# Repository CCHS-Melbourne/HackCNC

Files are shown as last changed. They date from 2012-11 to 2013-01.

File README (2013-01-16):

This repository is for the HackCNC project files.

HackCNC is a low-cost 2axis CNC machine developed for LCA2013 - Canberra.

It was developed and produced by members of hackmelbourne.org and freetronics.com.au

Hardware contains the development files for building the hackCNC frame.

Software contains the development and config files to compile the source code for the arduino and connect linuxcnc.

Docs has several documents and images that will help when assembling the kit.

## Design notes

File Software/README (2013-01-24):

This folder contains software elements useful in working with the HackCNC project. 

Libraries contains the arduino libraries needed to compile the EMCAruino sketch.

EMCArduino_07b_32u4 is the development firmware compatible with an Arduino based on a AT32u4 micro

NewLiquidCrystal is a control driver for using the attached LCD panel.

digitalWriteFast is a fast pin manipulation commands.

my-mill contains the connection and configuration files linuxcnc uses to connect to the arduino.  The simpilest place to put this in your home directory, then run linuxcnc with the command `linuxcnc my-mill.ini`

FunctionTest contains a basic sketch for testing high level components (serial communications, LCD, steppers, servo) without LinuxCNC.

----------
This software is based on the work of others. Attribution and other information can be found as follows:
digitalWriteFast - http://code.google.com/p/digitalwritefast/
EMCArduino - http://emc2arduino.wordpress.com/
LinuxCNC - http://www.linuxcnc.org/
NewLiquidCrystal - https://github.com/marcmerlin/NewLiquidCrystal

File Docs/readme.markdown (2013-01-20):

hackCNC

Conceptual Overview:


[Wiki page with assembly tips](http://www.arduinominiconf.org/index.php/HackCNC_Assembly_Tips)

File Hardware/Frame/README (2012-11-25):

These are the design files for the hackCNC project's frame.

This frame was designed to work with a material 6mm in depth.

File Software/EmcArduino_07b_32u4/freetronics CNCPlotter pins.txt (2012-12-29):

These are the pinouts for the Freetronics CNCPlotter board developed by Luke Weston.
This board is built around an Arduino Leonardo chip.
By default, the board is set to 8x microstepping.  This can be changed by soldering headers on the 3 pads for each driver board.
The CNCPlotter board only has two stepper drivers, with a servo for it's third axis.  An additional driver board can be connected to D5 and D13.

D0: UART RXD (not used, broken out to spare header)
D1: UART TXD (not used, broken out to spare header)
D2: LCD Strobe (Data loaded serially from AVR into 8-bit latch. Same as Pebble LCD hardware.)
D3: LCD Data
D4: LCD Clock
D5: Z-axis direction (not used in most cases)
D6: SD Card SPI chip select (active low). Standard SPI hardware (MOSI, MISO, SCK) used for SPI communications with SD card.
D7: Z-axis limit switch input (not used in most cases)
D8: Y-axis step signal
D9: Y-axis direction signal
D10: X-axis step signal
D11: X-axis direction signal
D12: Servo motor PWM position signal
D13: Z-axis step signal (not used usually)

A0: Touchscreen 1
A1: Touchscreen 2
A2: Touchscreen 3
A3: Touchscreen 4
A4: Y-axis limit switch input
A5: X-axis limit switch input

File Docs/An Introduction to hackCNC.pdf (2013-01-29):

## An Introduction to hackCNC

or -
hackCNC, a gateway drug for makers

or -
"What the hell is that whining noise?" - spouses everywhere

Presented by John Spencer - Linux Conf Australia - Canberra 2013

### What is hackCNC

hackCNC is a low cost, open source, two axis plotter.

It is desktop sized.

It is controlled by an Arduino processor and LinuxCNC.

It is cheap. This is important.

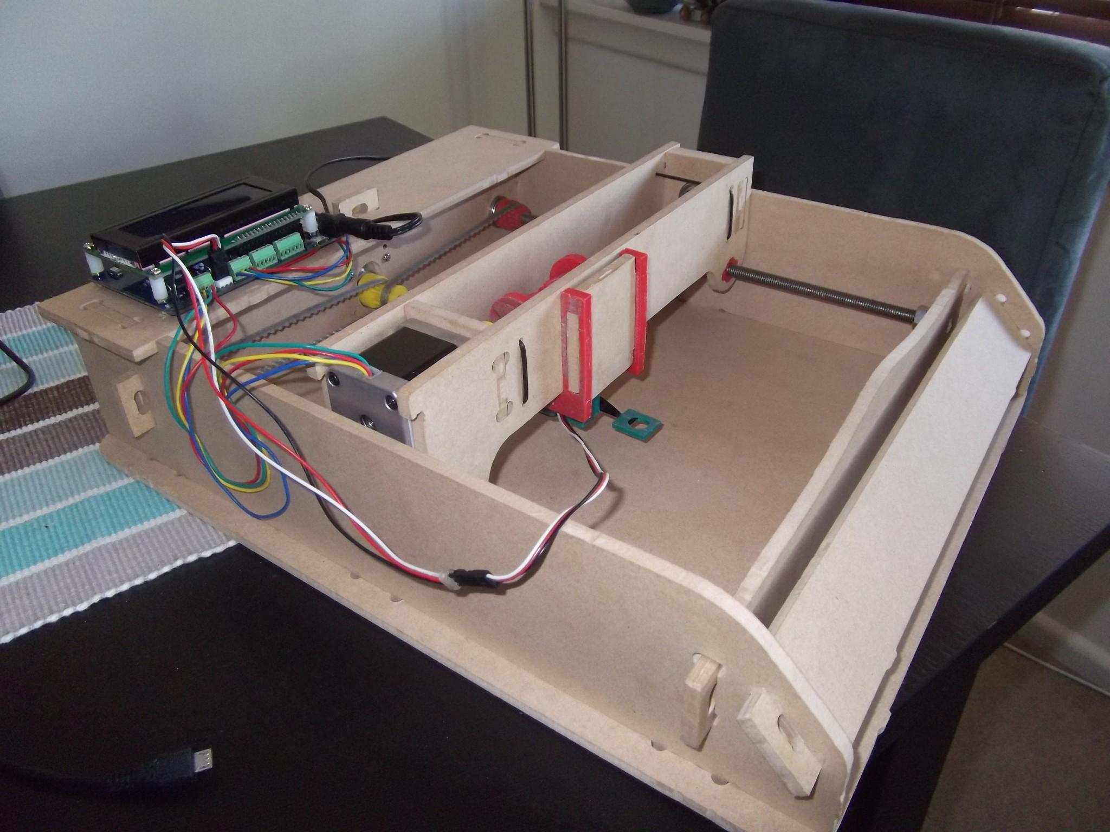
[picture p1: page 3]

### Why design/build something like hackCNC?

To get people interested in CNC.

To have something fun for groups like this one to build.

To give schools or special interest groups a nice easy project to work on.

### Limitations

Only 2 axis.
Threaded rods are a rough. Slow.
Noisy.
Small build area.
Only 50mm of vertical space.
3D parts take ~3.5 hours to make.

### How it was made - Frame

Designed on a completely not Open Source piece of software, let's call it Screw-up.

gCode generated on a different, also completely not Open Source piece of software, let's call that ... CAM-thingy.

Cut on my sort of Open Source home built CNC Router, running the totally FOSS linuxCNC.org!

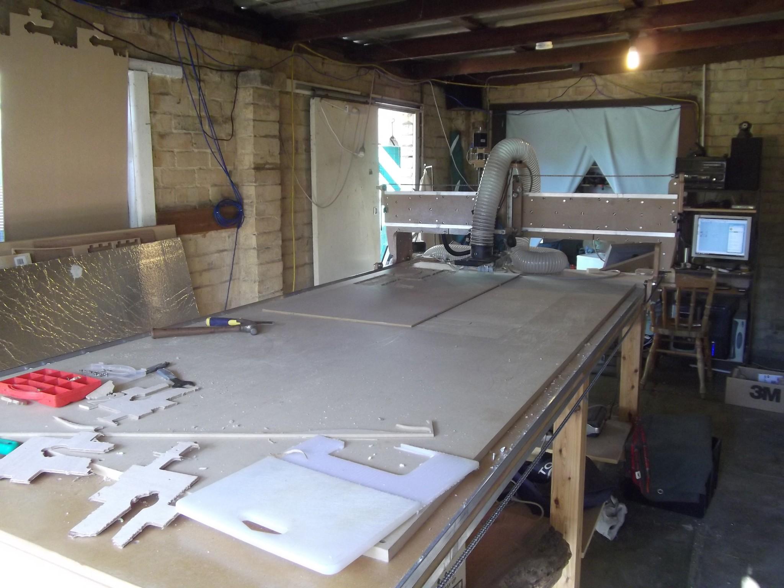
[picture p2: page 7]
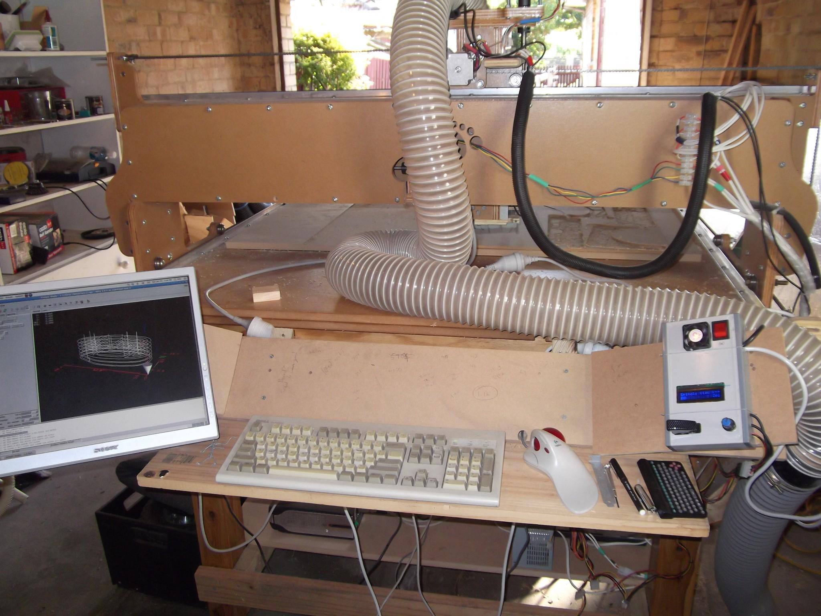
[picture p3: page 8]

### How it was made - Plastic

Also designed using Screw-up.

Cut into gCode using either slic3r.org or Cura.

Generously printed by members of the Melbourne Hackerspace. Mainly using Prusa 3D printers because they have a large enough build platform.

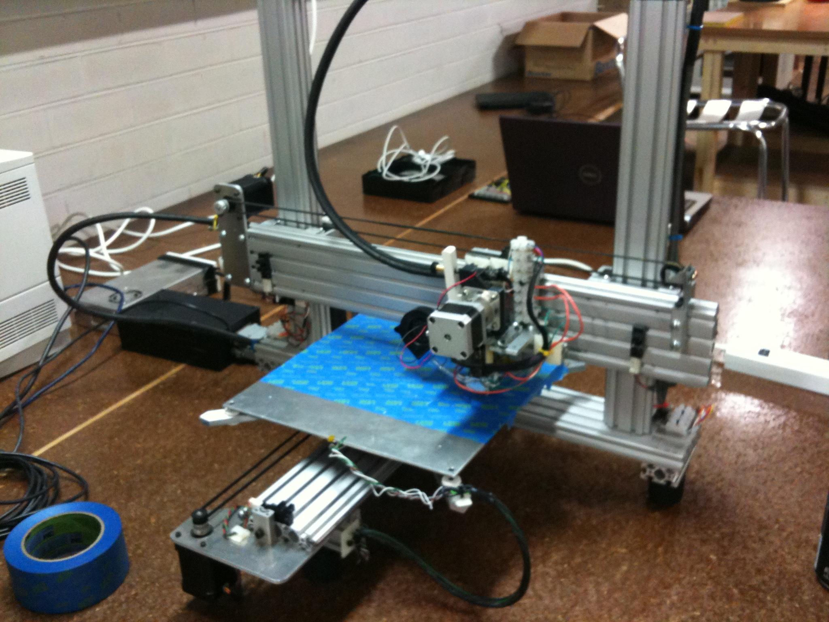
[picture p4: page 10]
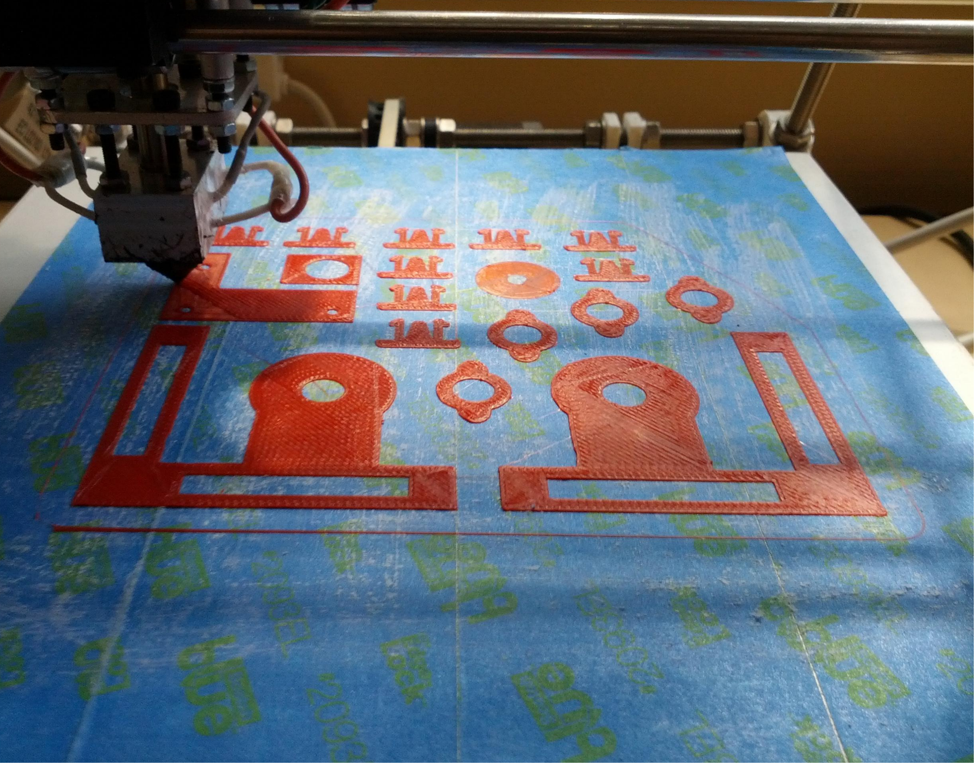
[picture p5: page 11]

### How it was made -Electronics/CNCPlot

Custom board designed by Luke Weston around the Arduino 32u4 (Leonardo) chip.

I'll let him talk about that.

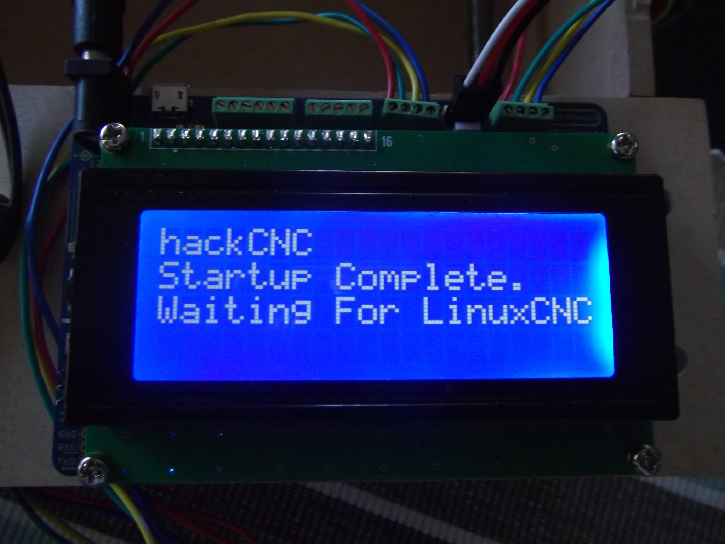
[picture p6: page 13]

### How it was made - all the other bits

Sourced by other Melbourne Hackerspace members, mostly from China and the US.

Software - How to make it do something.

Draw your plan in your favourite drawing program and load it into Inkscape.

Use the Export gCode tool. A negative Z axis movement of -0.8 works best.

Load your file in LinuxCNC.

### Great, NOW what do I do with it?

Just a few ideas I've heard :)

Frikken Laser Beams!!! (Sharks sold separately) Rotary Engraver.
Drag Cutter.
Two Colours.
Proper 3-axis (there is a breakout board) PCB engraving.
Simple 3D touch mapping.
Replace the threaded rod with belts and rails.
-- and, of course, you can re-use the electronics...

Contributors......so far.....

A big thank you to everyone who helped make this project possible. Here are most of the people who made this happen (I know I've missed some people....)

Freetronics/Jon Oxer
John Bosua
John Spencer
Luke Weston
Rob Brittain
Michael Sullivan
Andy Gelme
Bob Powers

Stuart Young
Angus Gratton
Don Douwsma
Ken Ihara
Josh Mesilane
Grant Diffey
George Patterson

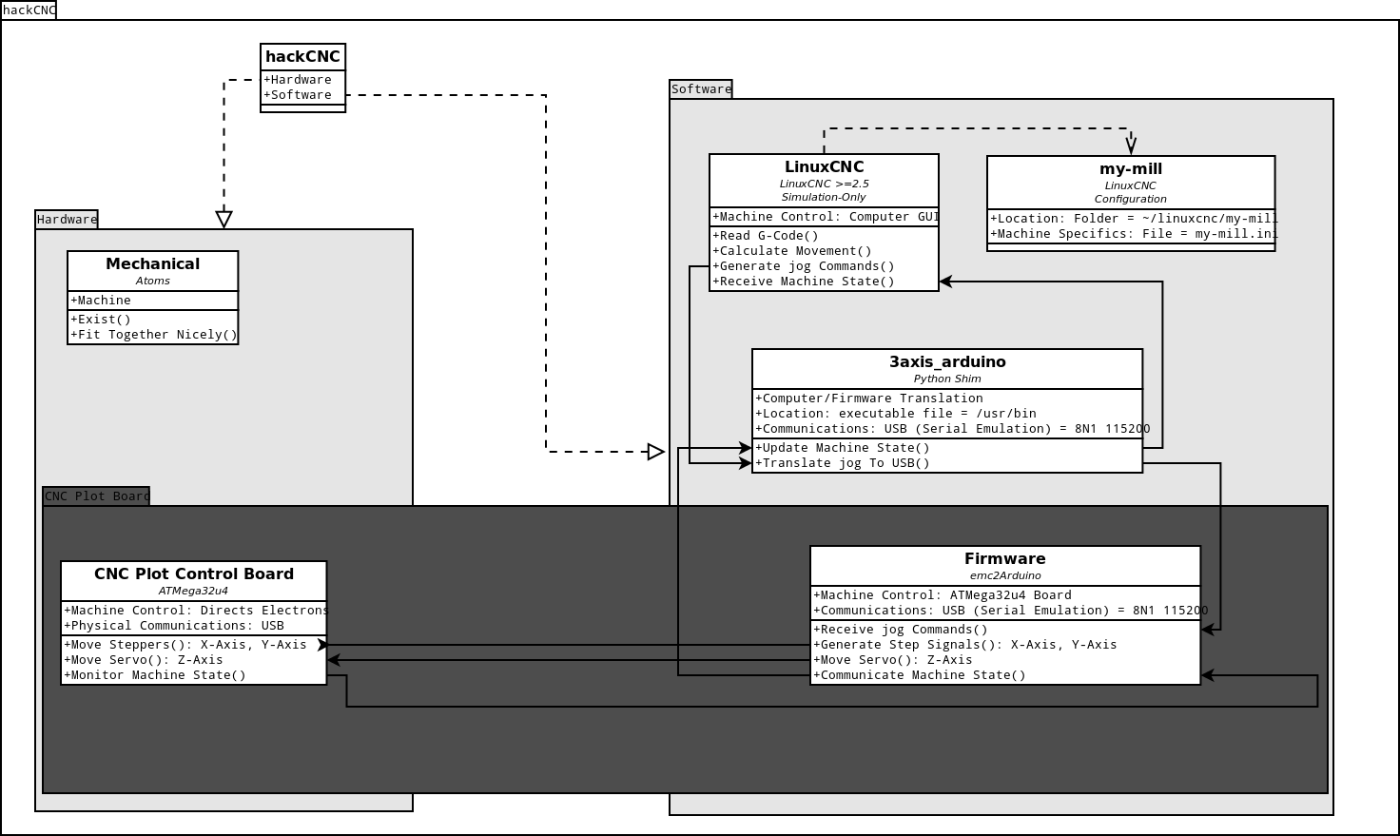
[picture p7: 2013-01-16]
Docs/Overview.png

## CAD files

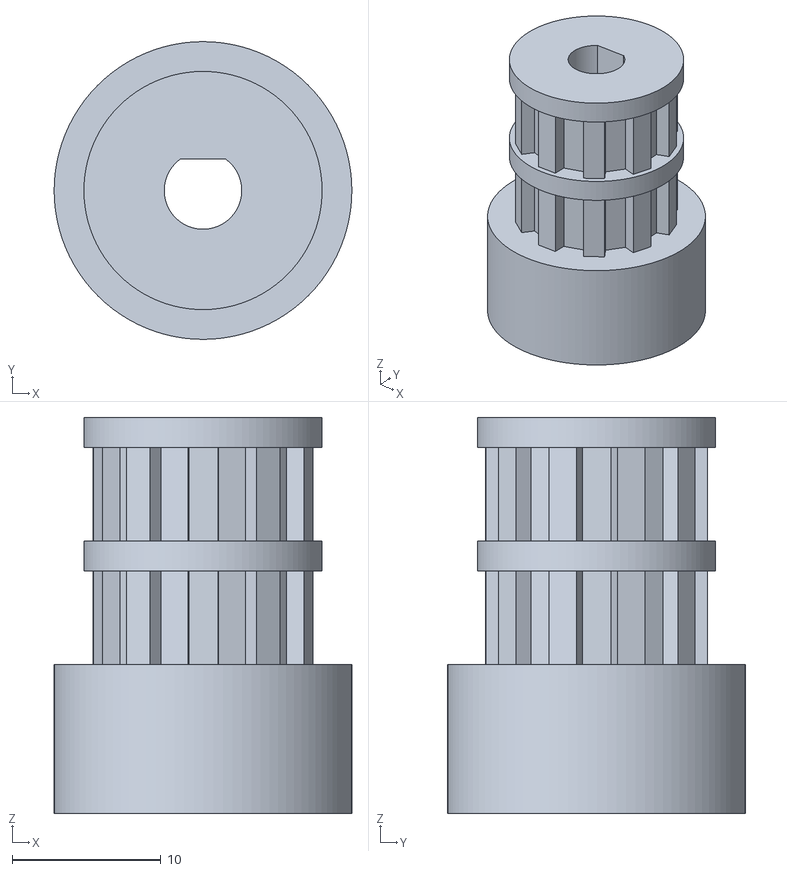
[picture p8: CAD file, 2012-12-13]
Hardware/3D Prints/5mm pulley.stl
20.0 x 20.0 x 26.6

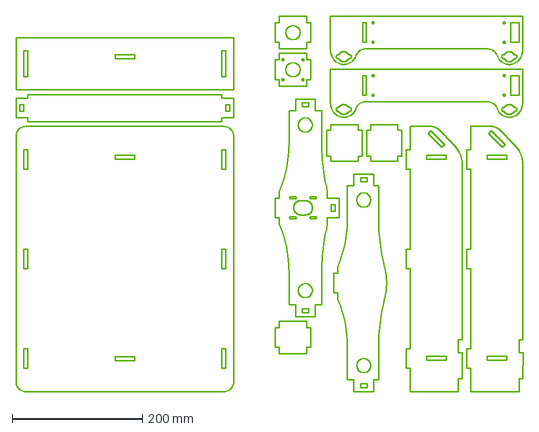
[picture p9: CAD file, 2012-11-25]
Hardware/Frame/hackCNC.dxf
778.0 x 576.0 mm

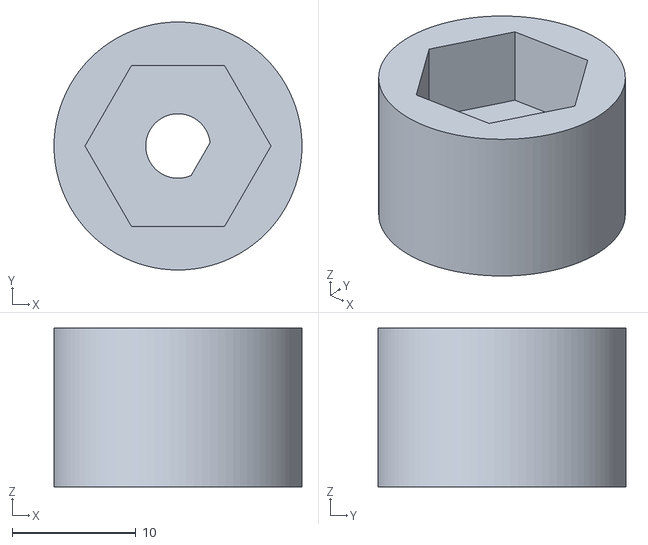
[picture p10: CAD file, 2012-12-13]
Hardware/3D Prints/shaft adapter.stl
20.0 x 20.0 x 12.8

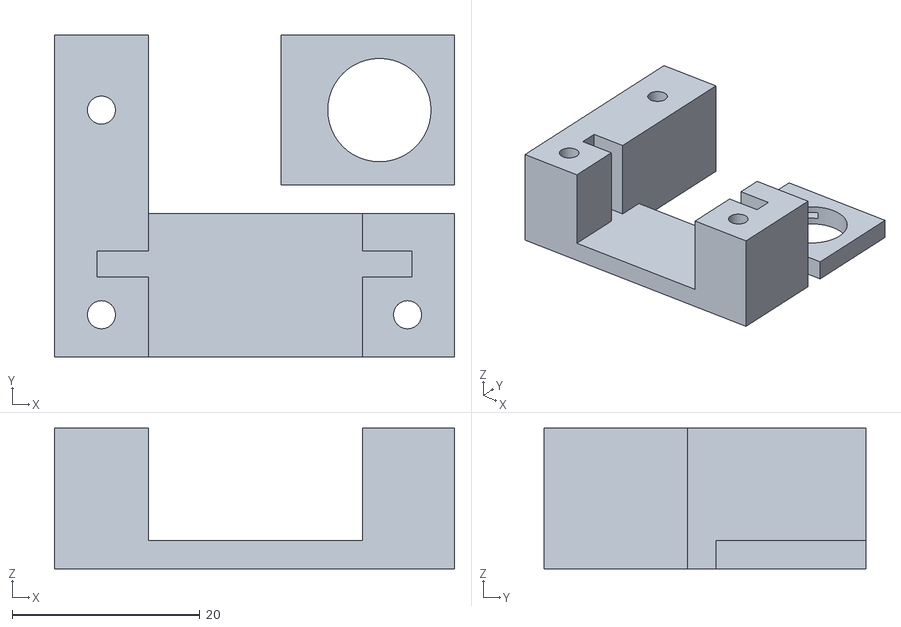
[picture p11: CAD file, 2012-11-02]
Hardware/3D Prints/Servo Holder-1.1.stl
42.6 x 34.3 x 15.0

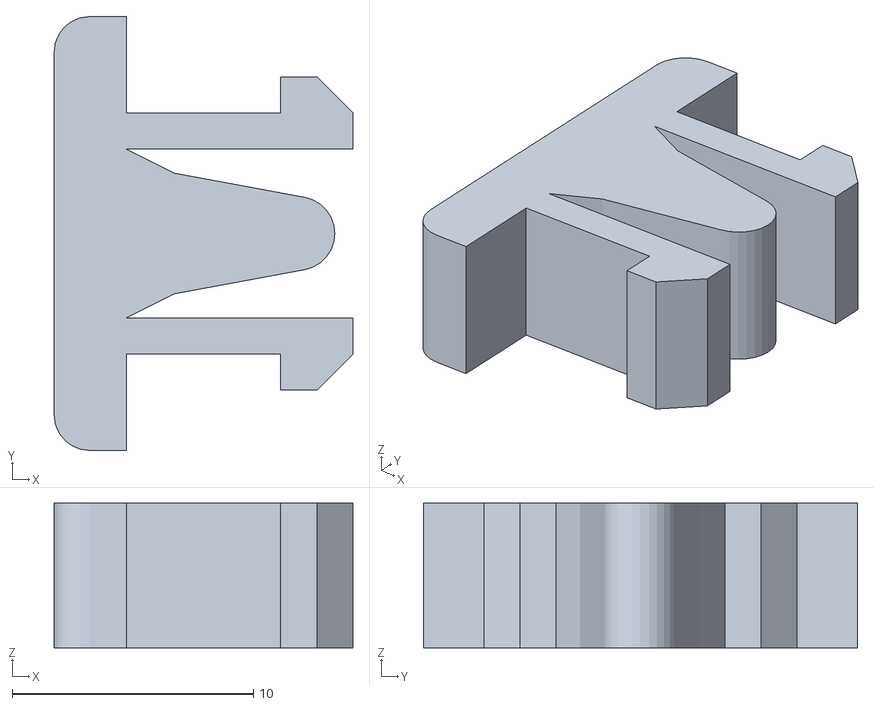
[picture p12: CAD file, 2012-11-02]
Hardware/3D Prints/Holding Pin.stl
12.4 x 18.0 x 6.00

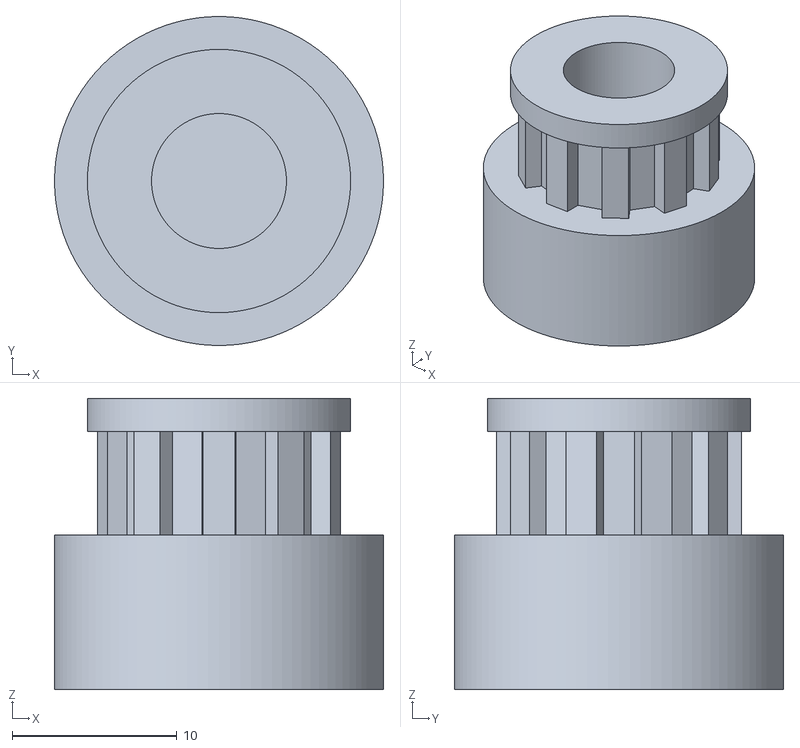
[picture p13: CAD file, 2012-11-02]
Hardware/3D Prints/8mm pulley.stl
20.0 x 20.0 x 17.7

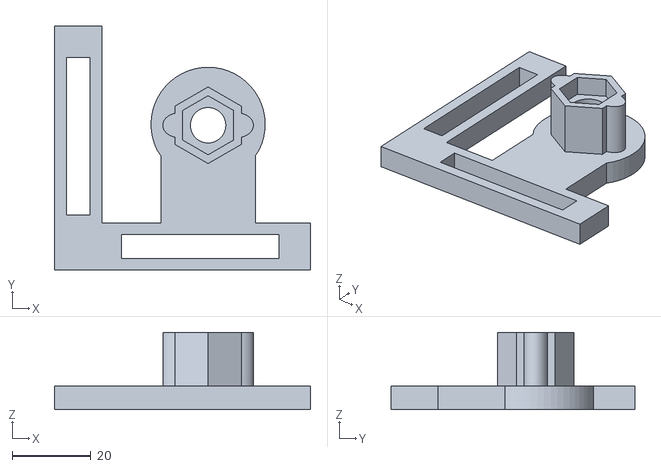
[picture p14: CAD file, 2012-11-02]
Hardware/3D Prints/Carriage 2.stl
65.0 x 62.0 x 19.6

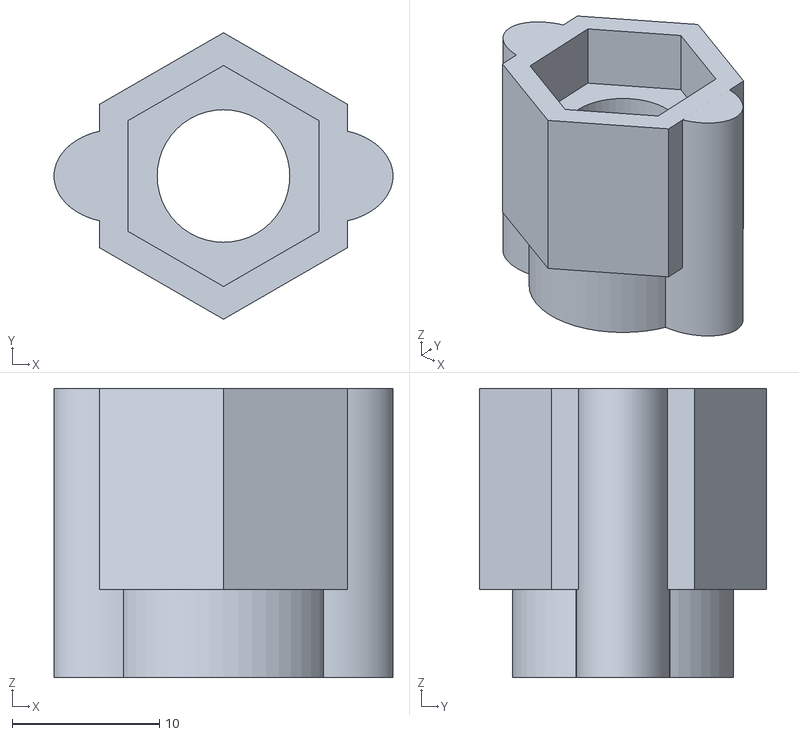
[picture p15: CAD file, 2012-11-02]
Hardware/3D Prints/Nut holder.stl
23.0 x 19.5 x 19.6

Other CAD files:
Hardware/3D Prints/Carriage 1.stl

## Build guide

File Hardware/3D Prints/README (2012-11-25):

"3D Print" quantities :-
1x 5mm pulley.stl
2x 8mm pulley.stl
1x Carriage 1.stl
1x Carriage 2.stl
9x Holding Pin.stl
4x Nut holder.stl
1x Servo Holder-1.1.stl
1x shaft adapter.stl

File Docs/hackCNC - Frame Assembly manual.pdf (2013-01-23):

## hackCNC

Frame Assembly Manual

Hints
1. If parts don't fit, first try turning them 90 degrees. A lot of them look square, but are actually rectangles (blame the designer).
2. Don't be afraid to try some brute force and ignorance. A lot of these parts are a VERY tight fit.
3. The wires on the stepper motors should be facing UP.
4. Without superglue on the nuts, this won't work. But don't worry, a pair of pliers will break the bond so you can break your hackCNC down for your trip home.

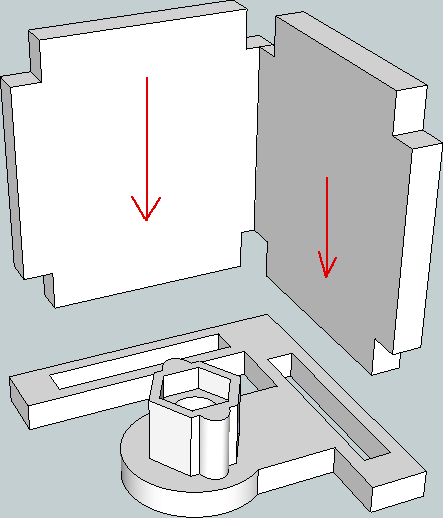
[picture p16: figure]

Section 1 : Z Axis Carriage | Section 1 : Step 1
| Parts 1 x 3D Printed Z Axis Bracket 2 x CNC Z Axis Plate

Section 1 : Step 2

Parts

1 x 8mm Long Nut

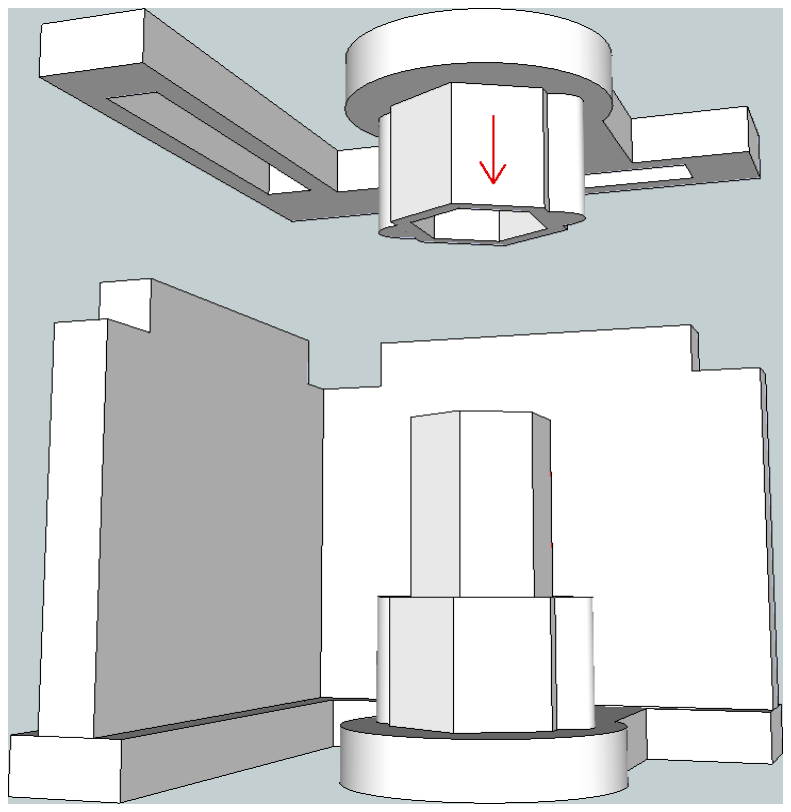
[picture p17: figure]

Section 1 : Step 3

Parts

1 x 3D Printed Z Axis Bracket

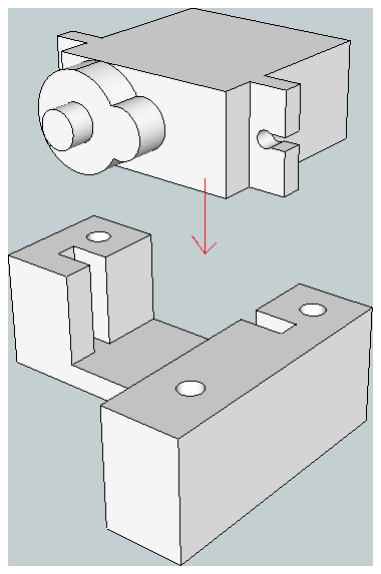
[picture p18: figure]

Section 1 : Step 4

Parts

1 x 3D Printed Servo Bracket 1 x 9g microservo

Section 1 : Step 5

Parts

2 x 4g Wood Screw

Section 1 : Step 6

Parts

1 x 4g Wood Screw
1 x Spring

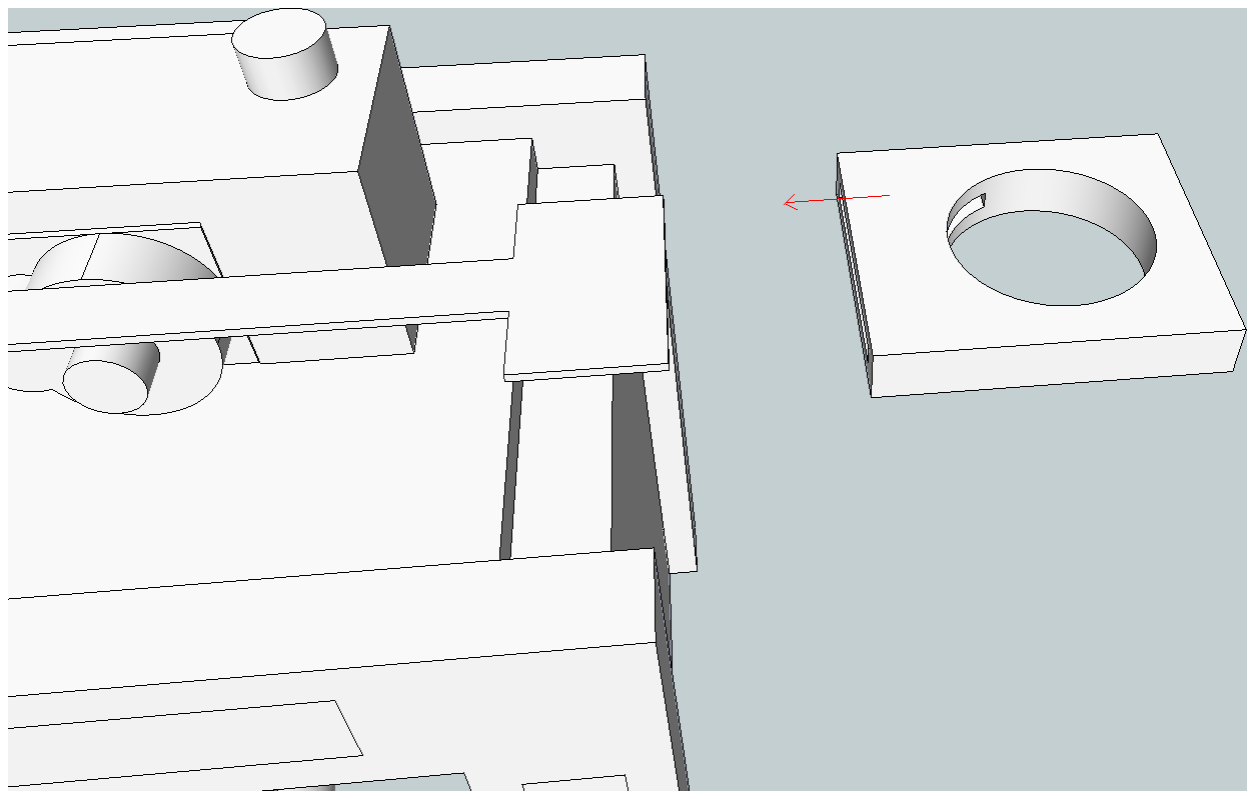
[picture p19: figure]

Section 1 : Step 7

Parts

1 x 3D Printed Pen Holder

Section 1 : Complete! | Section 2 : Y Axis Carriage

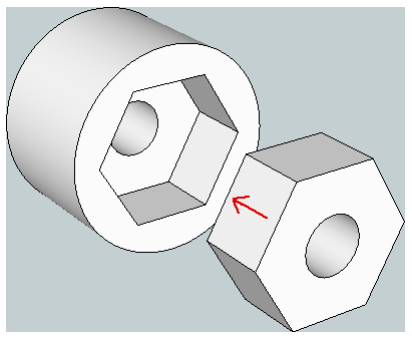
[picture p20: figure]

Section 2 : Step 1

Parts

1 x 3D Printed Y Axis Coupler 1 x 8mm nut

Section 2 : Step 2

Parts

1 x Nema 17 Stepper Motors 1 x CNC Y Axis Motor Mount 4 x 3mm Machine Screws

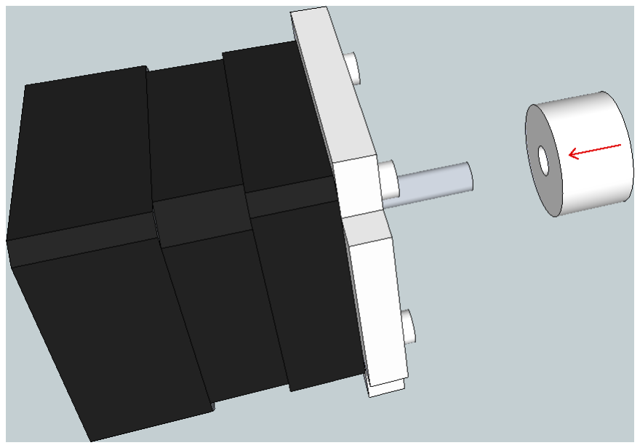
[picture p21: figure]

Section 2 : Step 3 | Section 2 : Step 4
| Parts 1 x 210 mm Long 8mm all-thread Part from Section 1

Section 2 : Step 4 - complete | Section 2 : Step 5
| Parts 1 x 8mm nuts Part from Section 2 : Step 4

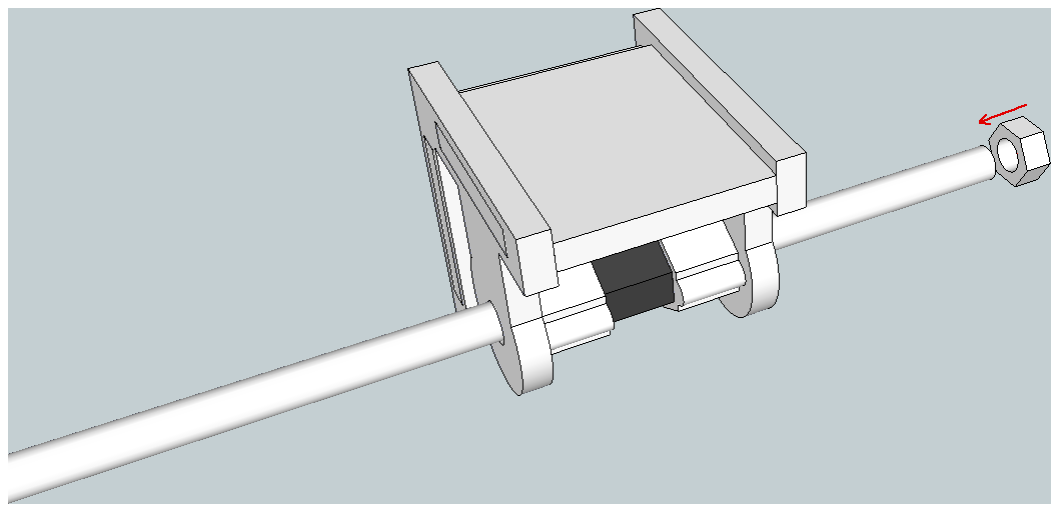
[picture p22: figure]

Section 2 : Step 6

Parts

1 x CNC Carriage Side
Part from Section 2 : Step 3

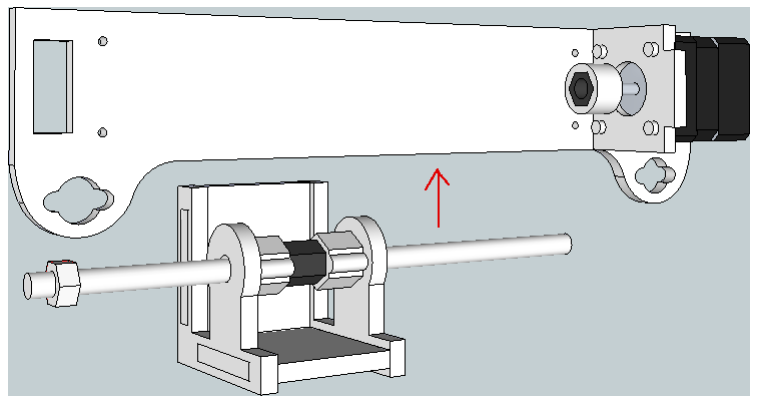
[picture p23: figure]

Section 2 : Step 7

Section 2 : Step 8

Superglue the end of the rod where it goes into the nut

Section 2 : Step 9

Parts

1 x CNC Y Axis Bearing Mount 1 x 608 bearing

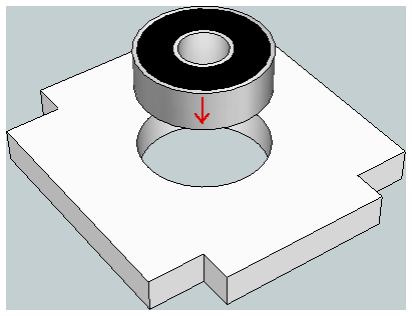
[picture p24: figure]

Section 2 : Step 10

Place an 8mm washer between the bearing and nut (not shown)

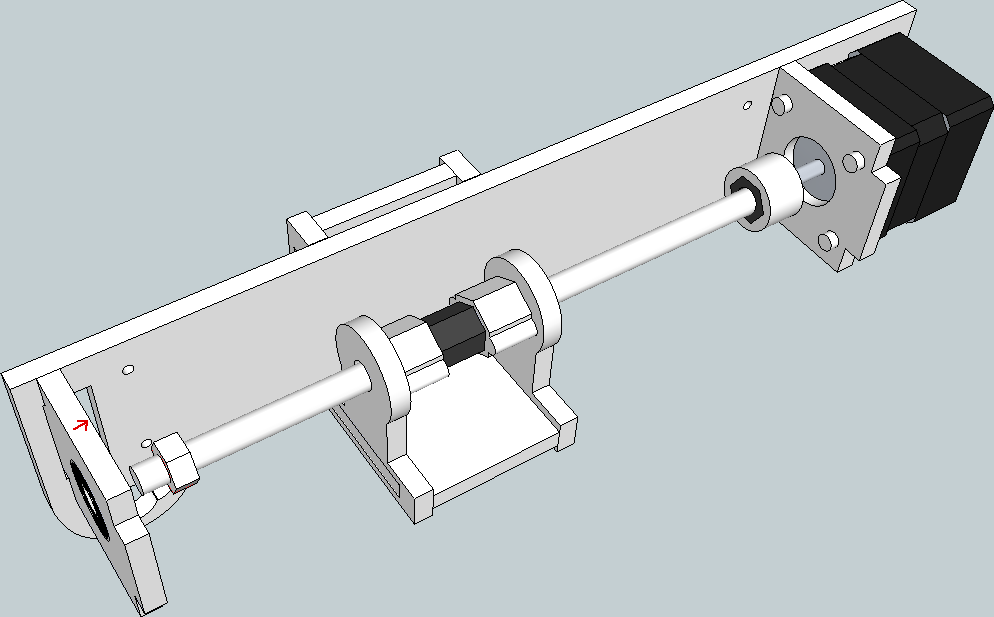
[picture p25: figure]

Section 2 : Step 11

Section 2 : Step 12

Parts

1 x CNC Y Axis Mount

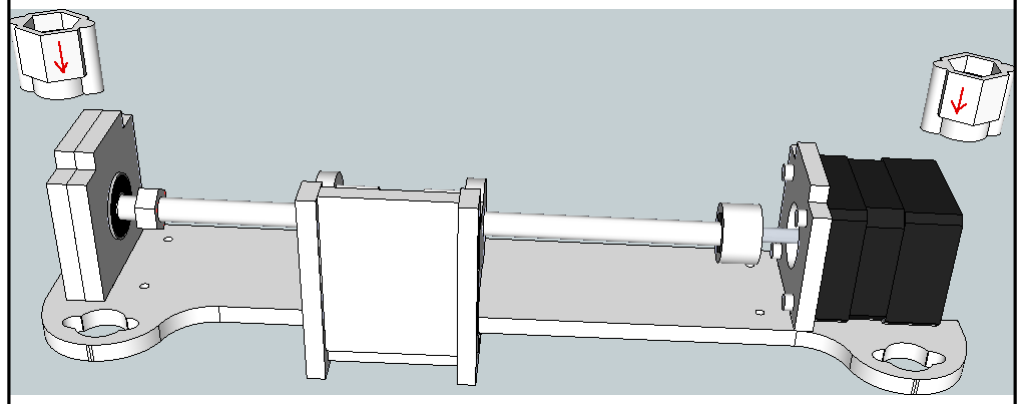
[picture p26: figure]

Section 2 : Step 13

Parts

2 x 3D Printed X Axis Nut Bracket

Section 2 : Step 14

Parts

2 x 8mm Long Nut

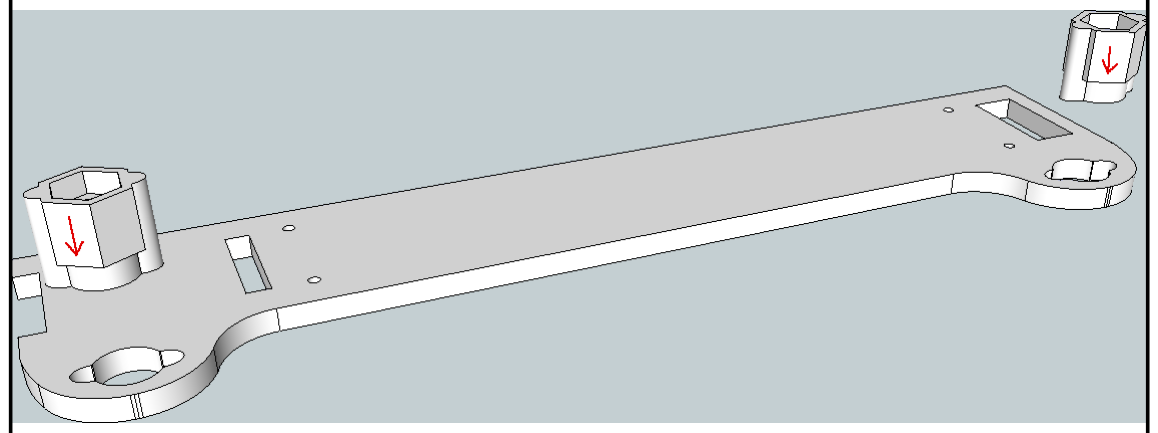
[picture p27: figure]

Section 2 : Step 15

Parts

1 x CNC Carriage Side
2 x 3D Printed X Axis Nut Bracket

Section 2 : Step 16 | Section 2 : Step 16 - Complete

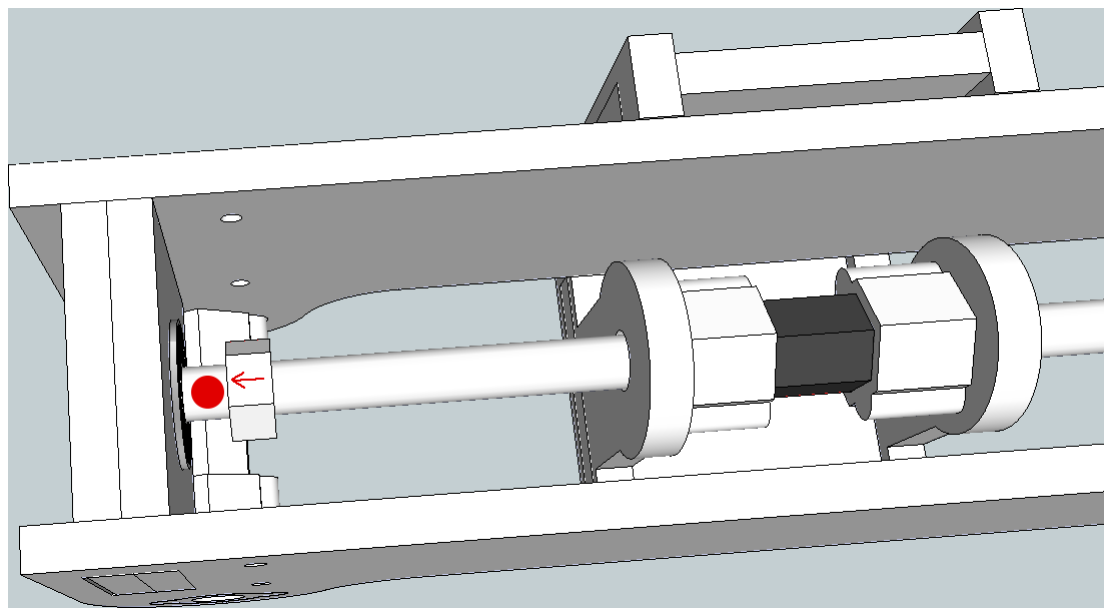
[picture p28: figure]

Section 2 : Step 17

Put a dob of glue before turning the nut

Section 2 : Complete!

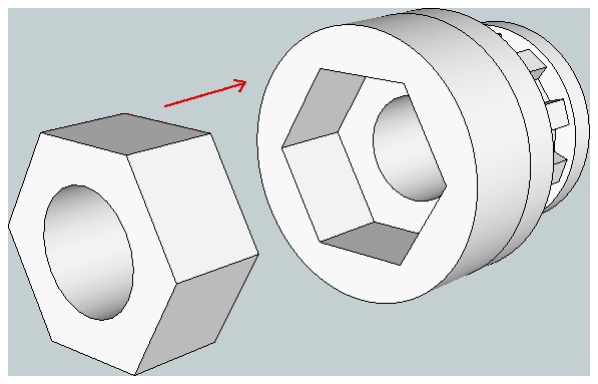
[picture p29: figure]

Section 3 : X Axis Rails | Section 3 : Step 1
| Parts 2 x 8mm nuts 2 x 3D Printed X Axis Gears

X 2

Section 3 : Step 1 - Complete | Section 3 : Step 2
| Parts 2 x 310mm long 8mm all-thread

Section 3 : Step 3

Parts

Part from Section 2

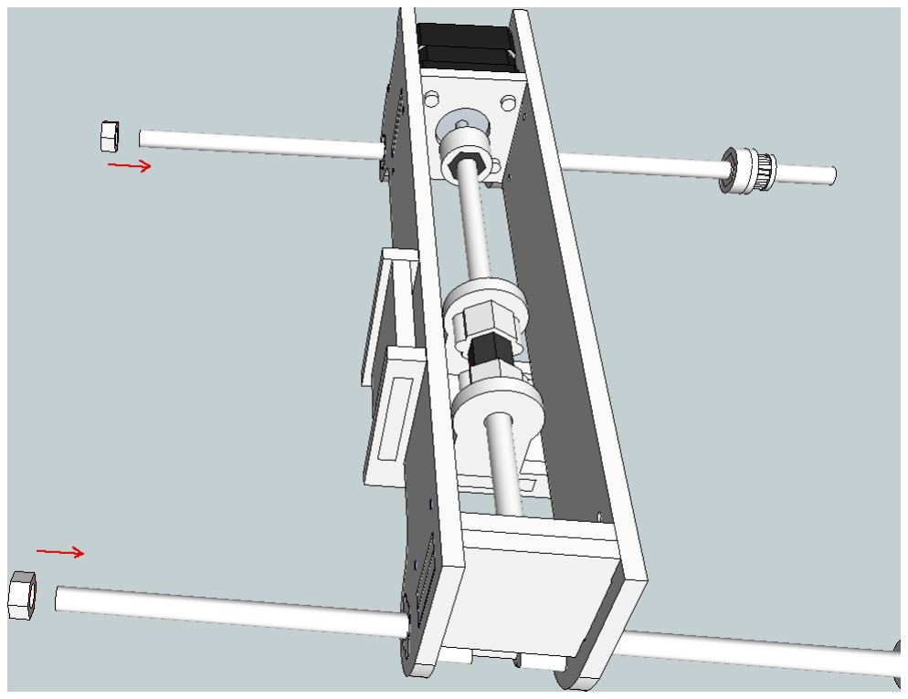
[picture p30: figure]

Section 3 : Step 4

Parts

2 x 8mm nuts

Section 3 : Complete! | Section 4 : Top Frame

Section 4 : Step 1

Parts

1 x Nema 17 Stepper Motor
4 x 3mm machine screws
1 x CNC Back Bulkhead

These should be somewhat loose.

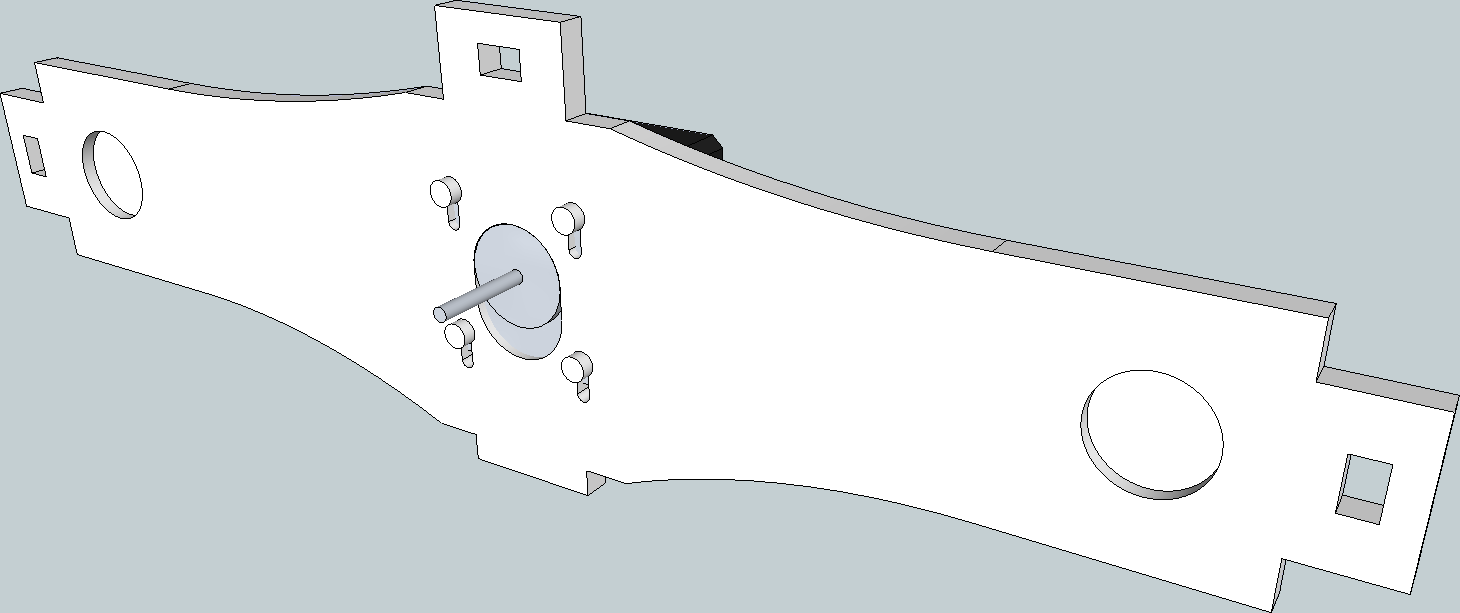
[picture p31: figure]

Section 4 : Step 1 - Complete

Section 4 : Step 2

Parts

1 x CNC Front Bulkhead
1 x CNC Side Plate
1 x CNC Front Plate

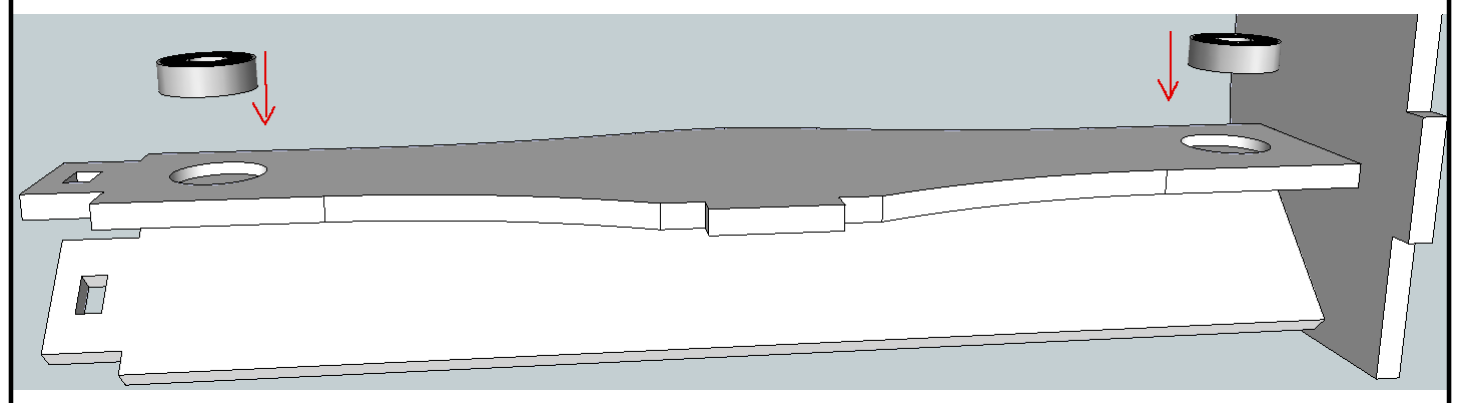
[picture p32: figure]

Section 4 : Step 3

Parts

2 x 608 bearings

Section 4 : Step 4

Parts

2 x 8mm Washers

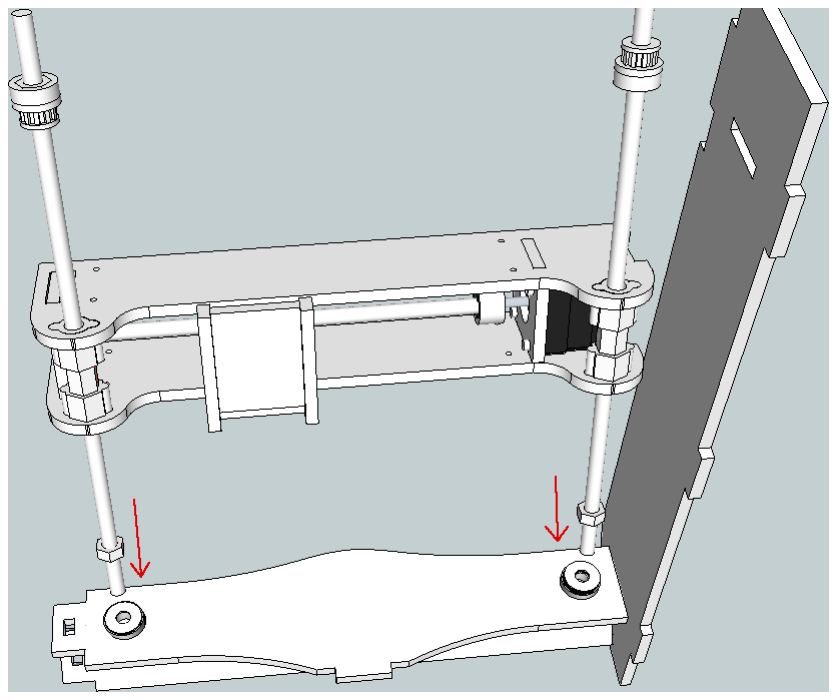
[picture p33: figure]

Section 4 : Step 5

Parts

Section 3

Section 4 : Step 6

Parts

2 x T5 Belts

Section 4 : Step 7

Parts

2 x 8mm Washers

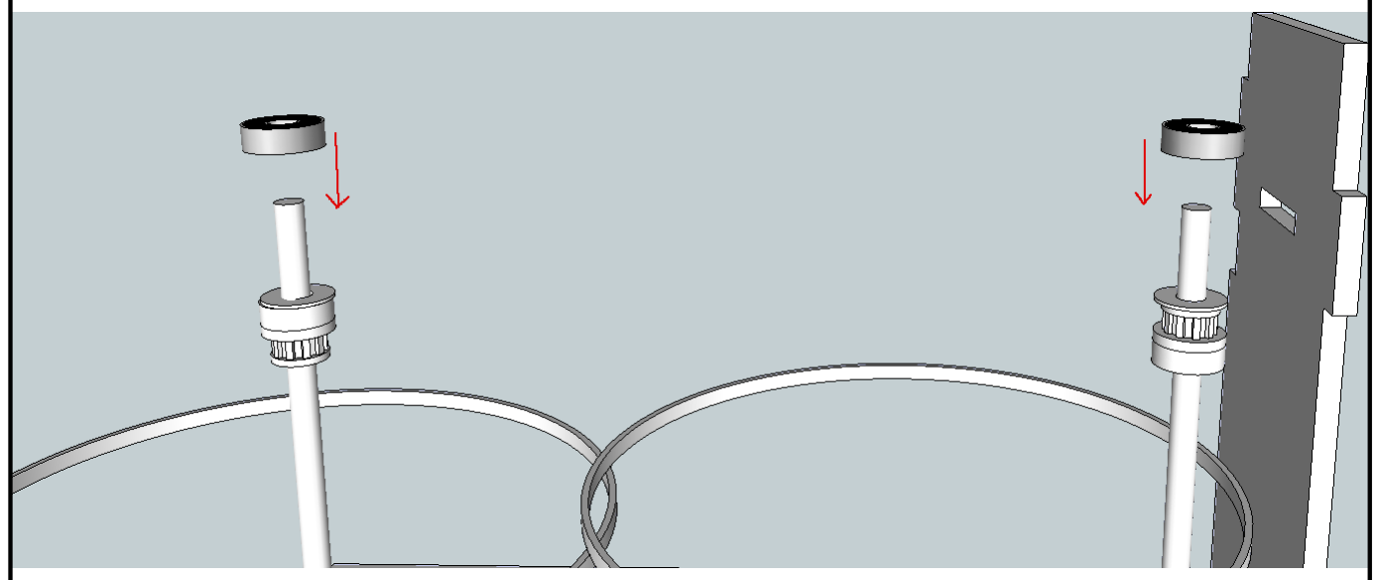
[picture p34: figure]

Section 4 : Step 8

Parts

2 x 608 Bearings

Section 4 : Step 9

Parts

Section 4 : Step 1 | You will need to wiggle these together a bit

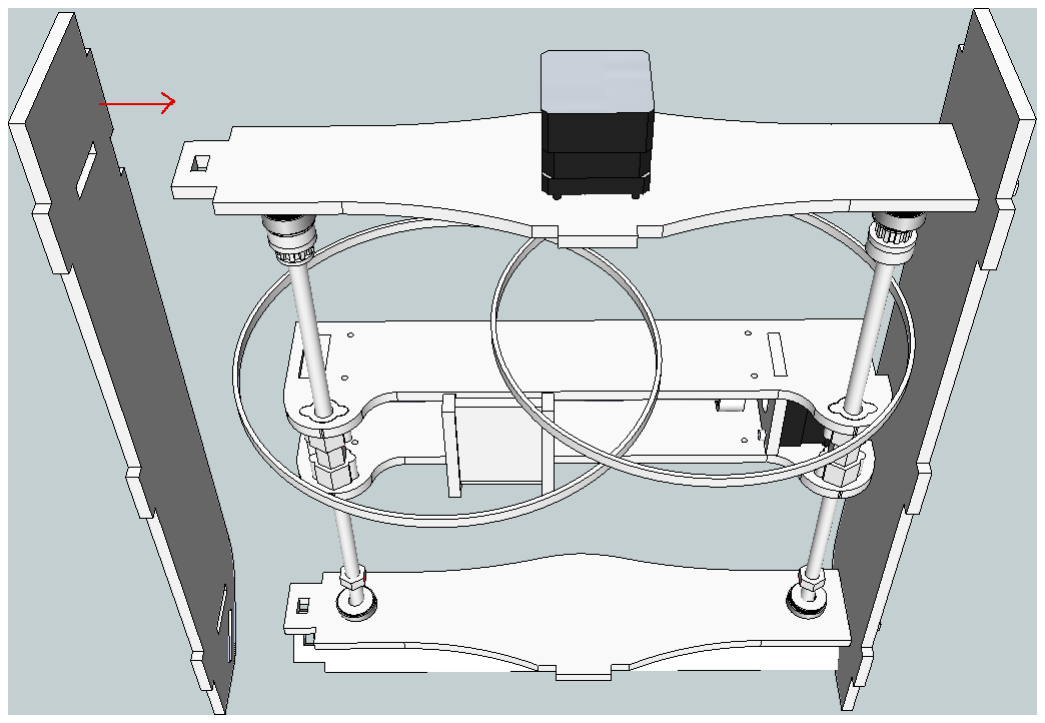
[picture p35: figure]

Section 4 : Step 10

Parts

1 x CNC Side Plate

Section 4 : Complete!

(Belts removed from view)

Section 5 : The Whole Frame

(Belts removed from view)

Section 5 : Step 1

Parts

1 x CNC Base Plate

The base plate only fits one way, you may need to spin it around.

Section 5 : Step 2 | Section 5 : Step 3

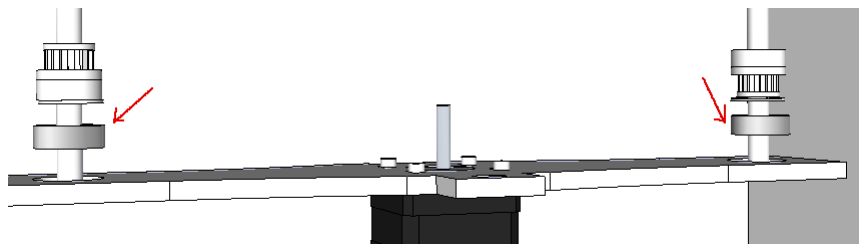
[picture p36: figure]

Section 5 : Step 4

Small dob of glue before doing up.

The all-thread should fit comfortably in the bearing, but not poke through the hole at the back (it is just for adjusting).

Section 5 : Step 5

Small dob of glue before doing up
There should be no slop, but the all-thread should move smoothly.

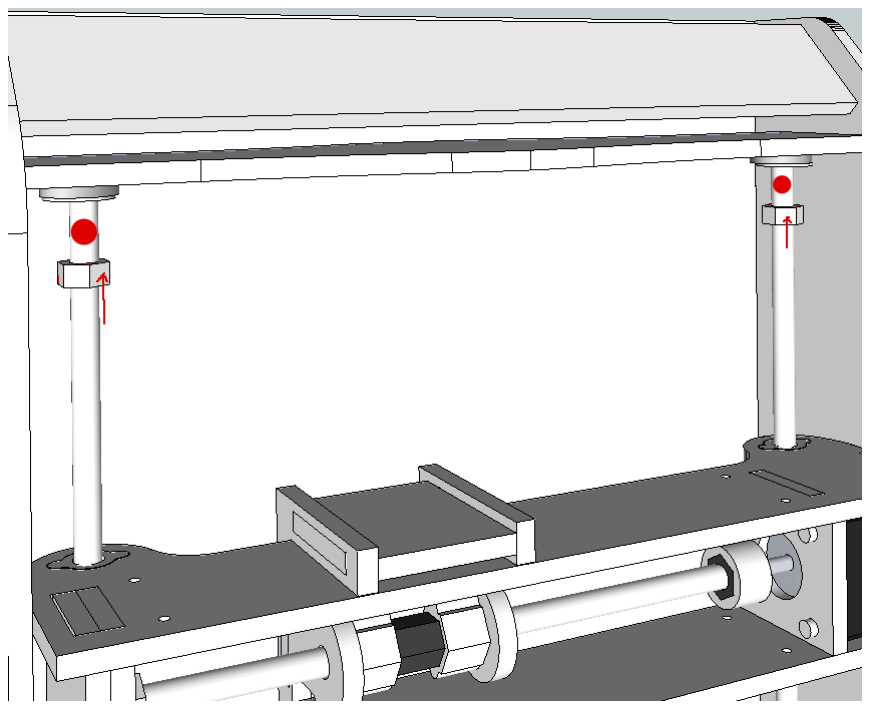
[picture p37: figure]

Section 5 : Step 6

Line up the teeth with the ones on the all-thread

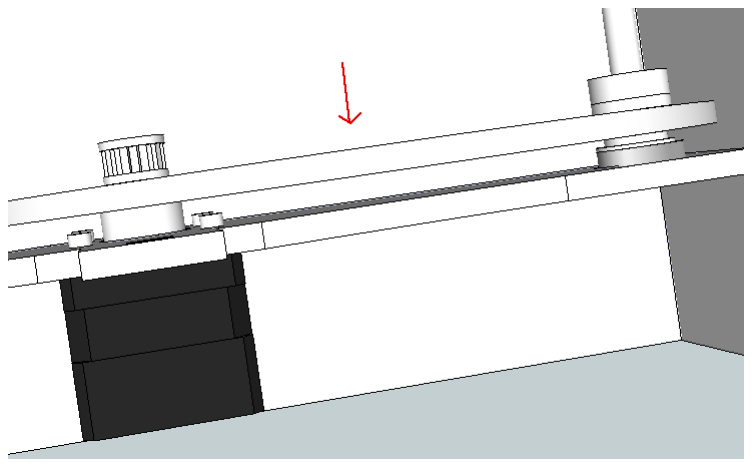
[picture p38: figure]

Section 5 : Step 7

You will have to turn the belt on.

Section 5 : Step 8

This belt will need turning on too. Before turning on, try to get the gantry level by rotating the all-thread. Turn on by rotating the stepper.

Section 5 : Step 9

(Belts magically invisible!)
Slide the stepper down to increase the tension on the belts.

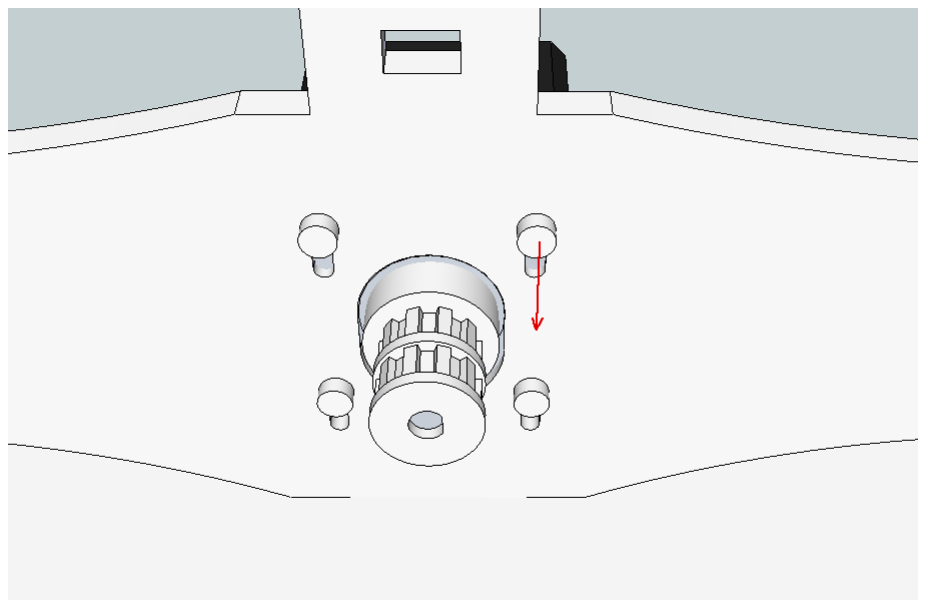
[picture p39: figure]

Section 5 : Step 10

Parts

1 x CNC Top Plate.

Section 5 : Complete!

Frame Complete!

Now to Assemble the Electronics.

Thank You

A big thank you to everyone who helped develop this project. Without everyone's contribution, it simply wouldn't be possible.

Andy Geleme
Jon Oxer
Shane Rogers
John Bosua
Dave Chanter
Rob Brittan
Bob Powers
Michael Sullivan
Stuart Young
Luke Weston

And all the crew at CCHS.

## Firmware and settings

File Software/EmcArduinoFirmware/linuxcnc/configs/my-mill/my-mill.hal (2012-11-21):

# Generated by stepconf at Fri Nov  2 20:51:22 2012
# If you make changes to this file, they will be
# overwritten when you run stepconf again
loadrt trivkins
loadrt [EMCMOT]EMCMOT base_period_nsec=[EMCMOT]BASE_PERIOD servo_period_nsec=[EMCMOT]SERVO_PERIOD num_joints=[TRAJ]AXES
#loadrt probe_parport
#loadrt hal_parport cfg="0x378 out  "
#setp parport.0.reset-time 5000
loadrt stepgen step_type=0,0,0
loadrt pwmgen output_type=1

#addf parport.0.read base-thread
addf stepgen.make-pulses base-thread
addf pwmgen.make-pulses base-thread
#addf parport.0.write base-thread
#addf parport.0.reset base-thread

addf stepgen.capture-position servo-thread
addf motion-command-handler servo-thread
addf motion-controller servo-thread
addf stepgen.update-freq servo-thread
addf pwmgen.update servo-thread

net spindle-cmd <= motion.spindle-speed-out => pwmgen.0.value
net spindle-on <= motion.spindle-on => pwmgen.0.enable
net spindle-pwm <= pwmgen.0.pwm
setp pwmgen.0.pwm-freq 100.0
setp pwmgen.0.scale 1166.66666667
setp pwmgen.0.offset 0.114285714286
setp pwmgen.0.dither-pwm true
net spindle-cw <= motion.spindle-forward

#net estop-out => parport.0.pin-01-out
#net xstep => parport.0.pin-02-out
#setp parport.0.pin-02-out-reset 1
#net xdir => parport.0.pin-03-out
#net ystep => parport.0.pin-04-out
#setp parport.0.pin-04-out-reset 1
#net ydir => parport.0.pin-05-out
#net zstep => parport.0.pin-06-out
#setp parport.0.pin-06-out-reset 1
#net zdir => parport.0.pin-07-out
#net astep => parport.0.pin-08-out
#setp parport.0.pin-08-out-reset 1
#net adir => parport.0.pin-09-out
#net spindle-cw => parport.0.pin-14-out
#net spindle-pwm => parport.0.pin-16-out
#net xenable => parport.0.pin-17-out




setp stepgen.0.position-scale [AXIS_0]SCALE
setp stepgen.0.steplen 1
setp stepgen.0.stepspace 0
setp stepgen.0.dirhold 3500
setp stepgen.0.dirsetup 3500
setp stepgen.0.maxaccel [AXIS_0]STEPGEN_MAXACCEL
net xpos-cmd axis.0.motor-pos-cmd => stepgen.0.position-cmd
net xpos-fb stepgen.0.position-fb => axis.0.motor-pos-fb
net xstep <= stepgen.0.step
net xdir <= stepgen.0.dir
net xenable axis.0.amp-enable-out => stepgen.0.enable

setp stepgen.1.position-scale [AXIS_1]SCALE
setp stepgen.1.steplen 1
setp stepgen.1.stepspace 0
setp stepgen.1.dirhold 350000
setp stepgen.1.dirsetup 350000
setp stepgen.1.maxaccel [AXIS_1]STEPGEN_MAXACCEL
net ypos-cmd axis.1.motor-pos-cmd => stepgen.1.position-cmd
net ypos-fb stepgen.1.position-fb => axis.1.motor-pos-fb
net ystep <= stepgen.1.step
net ydir <= stepgen.1.dir
net yenable axis.1.amp-enable-out => stepgen.1.enable

setp stepgen.2.position-scale [AXIS_2]SCALE
setp stepgen.2.steplen 1
setp stepgen.2.stepspace 0
setp stepgen.2.dirhold 35000
setp stepgen.2.dirsetup 35000
setp stepgen.2.maxaccel [AXIS_2]STEPGEN_MAXACCEL
net zpos-cmd axis.2.motor-pos-cmd => stepgen.2.position-cmd
net zpos-fb stepgen.2.position-fb => axis.2.motor-pos-fb
net zstep <= stepgen.2.step
net zdir <= stepgen.2.dir
net zenable axis.2.amp-enable-out => stepgen.2.enable

net estop-out <= iocontrol.0.user-enable-out
net estop-out => iocontrol.0.emc-enable-in

loadusr -W hal_manualtoolchange
net tool-change iocontrol.0.tool-change => hal_manualtoolchange.change
net tool-changed iocontrol.0.tool-changed <= hal_manualtoolchange.changed
net tool-number iocontrol.0.tool-prep-number => hal_manualtoolchange.number
net tool-prepare-loopback iocontrol.0.tool-prepare => iocontrol.0.tool-prepared

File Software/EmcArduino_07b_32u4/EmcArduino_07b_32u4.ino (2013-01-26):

/*
This work is public domain.
 
 This is a fork of https://github.com/dewy721/EMC-2-Arduino/downloads and has been heavily modified to:
 1. work with the arduino leonardo chipset.
 2. be simple for novice programmers to follow (possible futile)
 3. Work with mm
 4. Use a servo for it's z axis
 5. Support an LCD
 6. Support custom hardware https://github.com/lukeweston/CNCPlotter
 
 Work on this was mostly performed by John Spencer and Bob Powers.
 
 Please note: Although there are a LOT pin settings here.
 You can get by with as few as TWO pins per Axis. (dir & step)
 ie: 3 axies = 6 pins used. (minimum)
 9 axies = 18 pins or an entire UNO (using virtual limits switches only)
 This version is cut down to 3 axis.
 
 Note concerning switches: Be smart!
 AT LEAST use HOME switches.
 Switches are cheap insurance.
 You'll find life a lot easier if you use them entirely.
 
 If you choose to build with threaded rod for lead screws but leave out the switches
 You'll have one of two possible outcomes;
 You'll get tired really quickly of resetting the machine by hand.
 Or worse, you'll forget (only once) to reset it, and upon homing
 it WILL destroy itself while you go -> WTF!? -> OMG! -> PANIC! -> FACEPALM!
 
 List of axies. All 3 of them.
 AXIS_0 = X (Left/Right)
 AXIS_1 = Y (Near/Far) Lathes use this for tool depth.
 AXIS_2 = Z (Up/Down) Not typically used for lathes. Except lathe/mill combo.
 
 
 Remember, LinuxCNC sends out a bunch of stepper commands rather than an exact location
 This means tuning the speed LinuxCNC sends out commands is important.
 
 
 DYI robot builders: You can monitor/control this sketch via a serial interface.
 Example commands:
 
 jog x200;
 jog x-215.25 y1200 z0.002 a5;
 
 PS: If you choose to control this with your own interface then also modify the
 divisor variable further down.
 */

// You'll need this library. Get the interrupt safe version.
#include <digitalWriteFast.h> // http://code.google.com/p/digitalwritefast/
#include <LiquidCrystal_SR_LCD3.h> // https://github.com/marcmerlin/NewLiquidCrystal

#include <Servo.h> 

#include <avr/io.h>
#include <avr/interrupt.h>

//Servo settings MUST BE AN INT! BETWENEN 0-180
//servoDownZ is where your pen is engaged - pressing down 
#define servoDownZ 90
//servoUpZ is where your pen is disengaged - let up.
#define servoUpZ 160

// LCD Stuff
const int PIN_LCD_STROBE         =  2;  // Out: LCD IC4094 shift-register strobe
const int PIN_LCD_DATA           =  3;  // Out: LCD IC4094 shift-register data
const int PIN_LCD_CLOCK          =  4;  // Out: LCD IC4094 shift-register clock
LiquidCrystal_SR_LCD3 lcd(PIN_LCD_DATA, PIN_LCD_CLOCK, PIN_LCD_STROBE);

Servo myservo;
byte pos;

//#define BAUD    (115200)
#define BAUD 115200

// These will be used in the near future.
#define VERSION "00072.2"      // 5 characters seems arbitrary.  the .1 will give us an idea what version is uploaded to the arduino while we're developing.
#define ROLE    "hackCNC   " // 10 characters


//Pitch = mm/turn = 1.25 mm/turn
//mm/inch = 25.4
//turns/inch = 25.4/1.25 = 20.32
//turns/mm = 0.8
//steps/turn = 200
//fullsteps/inch = 200*20.32 = 4064
//fullsteps/mm = 200*0.8 = 160
//microstepping inch. 8 microsteps/step * 4064 = 32512 steps per in.
//microstepping mm. 8 microsteps/step / 0.8 = 1280 steps per mm.

#define stepsPerInchX 32512
#define stepsPerInchY 32512

#define stepsPerMmX 1280
#define stepsPerMmY 1280

//set very low because it's essentially digital, cutting down on z commands.
#define stepsPerInchZ 1
#define stepsPerMmZ 1

//#define minStepTime 25 //delay in MICROseconds between step pulses.
//#define minStepTime 625
// at 8x microstepping 1600 microsteps/rotation, so 625 = 1 rotation/sec
#define stepTime 77 // 8 rotations / second

// step pins (required)
#define stepPin0 10 //x step D10 - pin 30
#define stepPin1 8 //y step D8 - pin 28
#define stepPin2 -1 // z step

// dir pins (required)
#define dirPin0 11 //x dir D11 - pin 12
#define dirPin1 9 //y dir D9 - pin 29
#define dirPin2 -1 // z dir

// microStepping pins (optional)

#define chanXms1 -1
#define chanXms2 -1
#define chanXms3 -1
#define chanYms1 -1
#define chanYms2 -1
#define chanYms3 -1
#define chanZms1 -1
#define chanZms2 -1
#define chanZms3 -1

#define xEnablePin -1
#define yEnablePin -1
#define zEnablePin -1


#define useEstopSwitch  false
#define usePowerSwitch  false
#define useStartSwitch  false
#define useStopSwitch   false
#define usePauseSwitch  false
#define useResumeSwitch false
#define useStepSwitch   false

// Set to true if your using real switches for MIN positions.
#define useRealMinX false
#define useRealMinY false
#define useRealMinZ false

// Set to true if your using real switches for HOME positions.
#define useRealHomeX false
#define useRealHomeY false
#define useRealHomeZ false

// Set to false if your using real switches for MAX positions.
#define useRealMaxX false
#define useRealMaxY false
#define useRealMaxZ false

// If your using REAL switches you'll need real pins (ignored if using Virtual switches).
// -1 = not used.
#define xMinPin -1
#define yMinPin -1
#define zMinPin -1

#define xHomePin -1
#define yHomePin -1
#define zHomePin -1

#define xMaxPin -1
#define yMaxPin -1
#define zMaxPin -1

//#define powerSwitchIsMomentary true // Set to true if your using a momentary switch.
//#define powerPin    -1 // Power switch. Optional
//#define powerLedPin -1 // Power indicator. Optional

//#define eStopPin         -1 // E-Stop switch. You really, REALLY should have this one.
//#define eStopLedPin      -1 // E-Stop indicator. Optional

//#define startPin  -1 // CNC Program start switch.  Optional
//#define stopPin   -1 // CNC Stop program switch.   Optional
//#define pausePin  -1 // CNC Pause program switch.  Optional
//#define resumePin -1 // CNC Resume program switch. Optional
//#define stepPin   -1 // CNC Program step switch.   Optional

// Signal inversion for real switch users. (false = ground trigger signal, true = +5vdc trigger signal.)
// Note: Inverted switches will need pull-down resistors (less than 10kOhm) to lightly ground the signal wires.
#define xMinPinInverted false
#define yMinPinInverted false
#define zMinPinInverted false

#define xHomePinInverted false
#define yHomePinInverted false
#define zHomePinInverted false

#define xMaxPinInverted false
#define yMaxPinInverted false
#define zMaxPinInverted false

#define eStopPinInverted  false
#define powerPinInverted  false
#define probePinInverted  false
#define startPinInverted  false
#define stopPinInverted   false
#define pausePinInverted  false
#define resumePinInverted false
#define stepPinInverted   false

// Minimum position of virtual "homed" axes, in mm.  The HAL layer
// doesn't change its point of reference when homing, so we need to
// move the minimum positions so we know when we are at the home
// position
#define xMin 0
#define yMin 0
#define zMin -10

// Where should the VIRTUAL home switches be set to (ignored if using real switches).
// Set to whatever you specified in the StepConf wizard.
#define xHome 0
#define yHome 0
#define zHome 0

// Where should the VIRTUAL Max switches be set to (ignored if using real switches).
// Set to whatever you specified in the StepConf wizard.
// updated for mm
#define xMax 140
#define yMax 100
#define zMax 10

const bool giveFeedBackX = false;
const bool giveFeedBackY = false;
const bool giveFeedBackZ = false;

/*
  This indicator led will let you know how hard you pushing the Arduino.
 
 To test: Issue a G0 in the GUI command to send all axies to near min limits then to near max limits.
 Watch the indicator led as you do this. Adjust "Max Velocity" setting to suit.
 
 MOSTLY ON  = Pushing it too hard. Slow down! The Arduino can't cope, your CNC will break bits and make garbage.
 FREQUENT BLINK = Your a speed demon. Pushing it to the limits.
 OCCASIONAL BLINK = This is a safe speed. The best choice.
 OFF COMPLETELY = You can safely go faster.
 
 */
#define idleIndicator 13

// Invert direction of movement for an axis by setting to false.
boolean dirState0=true;
boolean dirState1=true;
boolean dirState2=true;

////////////////////////////////////////////////////////////////////////////////
/////////////////////////////END OF USER SETTINGS///////////////////////////////
////////////////////////////////////////////////////////////////////////////////

// This buffer's a single command.
char buffer[128];
int sofar;

// Offsets from HAL positions to real positions (in mm)
float xOffset;
float yOffset;
float zOffset;

float pos_x;
float pos_y;
float pos_z;

volatile boolean stepState=LOW;
volatile long stepper0Pos=0;
volatile long stepper0Goto=0;
volatile long stepper1Pos=0;
volatile long stepper1Goto=0;
volatile long stepper2Pos=0;
volatile long stepper2Goto=0;

boolean xMinState=false;
boolean yMinState=false;
boolean zMinState=false;

boolean xMinStateOld=false;
boolean yMinStateOld=false;
boolean zMinStateOld=false;

boolean xHomeState=false;
boolean yHomeState=false;
boolean zHomeState=false;

boolean xHomeStateOld=false;
boolean yHomeStateOld=false;
boolean zHomeStateOld=false;

boolean xMaxState=false;
boolean yMaxState=false;
boolean zMaxState=false;

boolean xMaxStateOld=false;
boolean yMaxStateOld=false;
boolean zMaxStateOld=false;


// no support for these at the moment
/*
boolean eStopStateOld=false;
 boolean powerStateOld=false;
 //boolean probeStateOld=false;
 boolean startStateOld=false;
 boolean stopStateOld=false;
 boolean pauseStateOld=false;
 boolean resumeStateOld=false;
 boolean stepStateOld=false;
 */

// Soft Limit and Power
boolean eStopState=false;
boolean powerState=false;

// Axis homed
boolean xHomed=false;
boolean yHomed=false;
boolean zHomed=false;

// this is a representation on how busy the arduino is.
// at 0 the arduino is idle, at 255 it is maxed out
volatile int globalBusy=0;

long divisor=1000000; // input divisor. Our HAL script wont send the six decimal place floats that EMC cranks out.
// A simple workaround is to multply it by 1000000 before sending it over the wire.
// So here we have to put the decimal back to get the real numbers.
// Used in: processCommand()

// these are feedback values
volatile float fbx=1;
volatile float fby=1;
volatile float fbz=1;

volatile float fbxOld=0;
volatile float fbyOld=0;
volatile float fbzOld=0;
volatile bool fbxTrigger = false;
volatile bool fbyTrigger = false;
volatile bool fbzTrigger = false;

// The current state of the program
// mainly used for the LCD
char runState='o'; // Off, Stopped, Running, Paused.

// Last update of the LCD panel.
unsigned long lastUpdate;

// These are dodgy hacks to tell the LCD to clear a line next cycle
boolean clearLine0 = false;
boolean clearLine1 = false;
boolean clearLine2 = false;
boolean clearLine3 = false;

//void jog(float x, float y, float z, float a, float b, float c, float u, float v, float w)
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
void loop()
{
  // These are all for physical switches, which we don't have
  //if(useEstopSwitch==true){boolean eStopState=digitalReadFast(eStopPin);if(eStopPinInverted){eStopState=!eStopState;}if(eStopState != eStopStateOld || eStopStateOld){eStopStateOld=eStopState;Serial.print("e");Serial.println(eStopState);delay(500);}}
  //if(usePowerSwitch==true){boolean powerState=digitalReadFast(powerPin);if(powerPinInverted){powerState=!powerState;}if(powerState != powerStateOld){powerStateOld=powerState;if(powerSwitchIsMomentary){Serial.println("pt");}else{Serial.print("p");Serial.println(powerState);}}}
  //if(useStartSwitch==true){boolean startState=digitalReadFast(startPin);if(startPinInverted){startState=!startState;}if(startState != startStateOld){startStateOld=startState;Serial.print("h");Serial.println(startState);}}
  //if(useStopSwitch==true){boolean stopState=digitalReadFast(stopPin);if(stopPinInverted){stopState=!stopState;}if(stopState != stopStateOld){stopStateOld=stopState;Serial.print("h");Serial.println(stopState+2);}}
  //if(usePauseSwitch==true){boolean pauseState=digitalReadFast(pausePin);if(pausePinInverted){pauseState=!pauseState;}if(pauseState != pauseStateOld){pauseStateOld=pauseState;Serial.print("h");Serial.println(pauseState+4);}}
  //if(useResumeSwitch==true){boolean resumeState=digitalReadFast(resumePin);if(resumePinInverted){resumeState=!resumeState;}if(resumeState != resumeStateOld){resumeStateOld=resumeState;Serial.print("h");Serial.println(resumeState+6);}}
  //if(useStepSwitch==true){boolean stepState=digitalReadFast(stepPin);if(stepPinInverted){stepState=!stepState;}if(stepState != stepStateOld){stepStateOld=stepState;Serial.print("h");Serial.println(stepState+8);}}


  // listen for serial commands
  while(Serial.available() > 0) {
    buffer[sofar++]=Serial.read();
    if(buffer[sofar-1]==';') break;  // in case there are multiple instructions
  }

  // Received a "+" turn something on.
  // Setting LCD status information here won't slow down processing.
  if(sofar>0 && buffer[sofar-3]=='+') {

    //if(sofar>0 && buffer[sofar-2]=='P') { /* Power LED & PSU   ON */ if(powerLedPin>0){digitalWriteFast(powerLedPin,HIGH);}if(powerSupplyPin>0){digitalWriteFast(powerSupplyPin,psuState);}}
    if(sofar>0 && buffer[sofar-2]=='E') { eStopState=true; lcd.setCursor (0, 1); lcd.print(F("eStop Open.         "));lcd.setCursor (15, 0); lcd.print(F("E"));};
    if(sofar>0 && buffer[sofar-2]=='P') { powerState=true; lcd.setCursor (0, 1); lcd.print(F("Power Initialised.  "));lcd.setCursor (16, 0); lcd.print(F("P"));};
    //if(sofar>0 && buffer[sofar-2]=='E') { /* E-Stop Indicator  ON */ if(eStopLedPin>0){digitalWriteFast(eStopLedPin,HIGH);}}

    // Running code state
    // These are mutually exclusive so don't need a - set.
    // On startup, don't set these.  purely to look cooler on the lcd
    // Should be a better way
    if(sofar>0 && buffer[sofar-2]=='r') { runState = 'r'; lcd.setCursor (12, 0); lcd.print(F("R"));lcd.setCursor (0, 1); lcd.print(F("Running gCode       "));lcd.setCursor (0, 2);lcd.print(F("Touch to PAUSE      "));};
    // extra check to make sure the machine wasn't off.
    if(sofar>0 && buffer[sofar-2]=='s' && runState!='o' ) { runState = 's'; lcd.setCursor (12, 0); lcd.print(F("S"));lcd.setCursor (0, 1); lcd.print(F("Run Stopped!        "));lcd.setCursor (0, 2);lcd.print(F("                    "));};
    if(sofar>0 && buffer[sofar-2]=='p') { runState = 'r'; lcd.setCursor (12, 0); lcd.print(F("P"));lcd.setCursor (0, 1); lcd.print(F("Run Paused!         "));lcd.setCursor (0, 2);lcd.print(F("Touch to RESUME     "));};


    // homing
    if(sofar>0 && buffer[sofar-2]=='0') { xHomed=true; xOffset = pos_x; lcd.setCursor (0, 1); lcd.print(F("X axis Homed        "));lcd.setCursor (17, 0); lcd.print(F("X"));};
    if(sofar>0 && buffer[sofar-2]=='1') { yHomed=true; yOffset = pos_y; lcd.setCursor (0, 1); lcd.print(F("Y axis Homed        "));lcd.setCursor (18, 0); lcd.print(F("Y"));};
    if(sofar>0 && buffer[sofar-2]=='2') { zHomed=true; zOffset = pos_z; lcd.setCursor (0, 1); lcd.print(F("Z axis Homed        "));lcd.setCursor (19, 0); lcd.print(F("Z"));};

    // reset the buffer
    sofar=0;  
  }

  // Received a "-" turn something off.
  // we have no physical pins, just software
  // so this is mostly not needed.
  if(sofar>0 && buffer[sofar-3]=='-') {
    //if(sofar>0 && buffer[sofar-2]=='P') { /* Power LED & PSU   OFF */ if(powerLedPin>0){ digitalWriteFast(powerLedPin,LOW);}if(powerSupplyPin>0){digitalWriteFast(powerSupplyPin,!psuState);}}
    if(sofar>0 && buffer[sofar-2]=='E') { eStopState=false; lcd.setCursor (0, 1); lcd.print(F("eStop ACTIVE! Halted"));lcd.setCursor (15, 0); lcd.print(F("_"));};
    if(sofar>0 && buffer[sofar-2]=='P') { powerState=false; lcd.setCursor (0, 1); lcd.print(F("Power Down.         "));lcd.setCursor (16, 0); lcd.print(F("_"));};

    //if(sofar>0 && buffer[sofar-2]=='E') { /* E-Stop Indicator  OFF */ if(eStopLedPin>0){digitalWriteFast(eStopLedPin,LOW);}}

    if(sofar>0 && buffer[sofar-2]=='0') { xHomed=false; lcd.setCursor (0, 1); lcd.print(F("X axis Unhomed      "));lcd.setCursor (17, 0); lcd.print(F("_"));};
    if(sofar>0 && buffer[sofar-2]=='1') { yHomed=false; lcd.setCursor (0, 1); lcd.print(F("Y axis Unhomed      "));lcd.setCursor (18, 0); lcd.print(F("_"));};
    if(sofar>0 && buffer[sofar-2]=='2') { zHomed=false; lcd.setCursor (0, 1); lcd.print(F("Z axis Unhomed      "));lcd.setCursor (19, 0); lcd.print(F("_"));};


    // clear the buffer.
    // this means we'll skip the processCommand step
    sofar=0;
  }

  // Received a "?" about something give an answer.
  if(sofar>0 && buffer[sofar-3]=='?') {
    if(sofar>0 && buffer[sofar-2]=='V') { 
      /* Report version */
      Serial.println(VERSION);
      lcd.setCursor (0, 3);
      lcd.print(F(VERSION));
      lcd.print(F("            ")); // match the Version length.  Cheating
    }
    if(sofar>0 && buffer[sofar-2]=='R') {
      /* Report role    */
      Serial.println(ROLE);
      lcd.setCursor (0, 3);
      lcd.print(F(ROLE));
      lcd.print(F("          ")); // match the Role length.  Cheating
    }

    // clear the buffer.
    // this means we'll skip the processCommand step
    sofar=0;
  }

  // if we hit a semi-colon, assume end of instruction.
  // Do NOT EXECUTE instructions if E-STOP or Power is off!
  // eStopState is not implemented yet.   awesome :(
  if(powerState && eStopState && sofar>0 && buffer[sofar-1]==';') {

    buffer[sofar]=0;

    // do something with the command
    processCommand();

    // reset the buffer
    sofar=0;
  }

  // globalBusy is all well and good, but if the machine is working it will never update.
  // We have to find a good balance between performance and update cycle
  // Split this up due to some weirdness using all three values
  if(powerState && eStopState)
  {
    // update every second (1000).  Adjust this value
    // shouldn't need to update the X:, Y: and Z: bits every iteration
    // just update the numbers.
    // X and Y values should be trimmed/padded to 5 characters.  z to 4
    if (lastUpdate < (millis() - 1000) || globalBusy<1 )
    {

      lcd.setCursor (0, 3);
      lcd.print(F("X:"));
      lcd.print(pos_x-xOffset,1);
      lcd.setCursor (7, 3);
      lcd.print(F("Y:"));
      lcd.print(pos_y-yOffset,1);
      lcd.setCursor (14, 3);
      lcd.print(F("Z:"));
      lcd.print(pos_z-zOffset,1);

      lastUpdate = millis();
    }
  }

  // Check if we need to send end-of-move feedback to linuxcnc
  // (this feedback isn't currently used upstream in the HAL)
  if(fbxTrigger){
    Serial.print("fx");
    Serial.println(fbx,6);
    fbxTrigger = false;
  }
  if(fbyTrigger) {
    Serial.print("fy");
    Serial.println(fby,6);
    fbyTrigger = false;
  }
}

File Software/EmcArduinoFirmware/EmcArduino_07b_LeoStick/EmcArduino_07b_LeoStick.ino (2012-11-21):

/*
This work is public domain.

Please note: Although there are a LOT pin settings here.
You can get by with as few as TWO pins per Axis. (dir & step)
ie: 3 axies = 6 pins used. (minimum)
    9 axies = 18 pins or an entire UNO (using virtual limits switches only)

Note concerning switches: Be smart!
  AT LEAST use HOME switches.
  Switches are cheap insurance.
  You'll find life a lot easier if you use them entirely.
  
  If you choose to build with threaded rod for lead screws but leave out the switches
  You'll have one of two possible outcomes;
    You'll get tired really quickly of resetting the machine by hand.
    Or worse, you'll forget (only once) to reset it, and upon homing
    it WILL destroy itself while you go -> WTF!? -> OMG! -> PANIC! -> FACEPALM!

 List of axies. All 9 of them.
     AXIS_0 = X (Left/Right)
     AXIS_1 = Y (Near/Far) Lathes use this for tool depth.
     AXIS_2 = Z (Up/Down) Not typically used for lathes. Except lathe/mill combo.
     AXIS_3 = A (Rotation parallel to X axis) lathe chuck.
     AXIS_4 = B (Rotation parallel to Y axis)
     AXIS_5 = C (Rotation parallel to Z axis)
     AXIS_6 = U (Rotation perpendicular to X axis)
     AXIS_7 = V (Rotation perpendicular to Y axis)
     AXIS_8 = W (Rotation perpendicular to Z axis)

  DYI robot builders: You can monitor/control this sketch via a serial interface.
  Example commands:
  
    jog x200;
    jog x-215.25 y1200 z0.002 a5;
    
    PS: If you choose to control this with your own interface then also modify the
    divisor variable further down.
*/

// You'll need this library. Get the interrupt safe version.
#include <digitalWriteFast.h> // http://code.google.com/p/digitalwritefast/


#include <Servo.h> 

//MUST BE AN INT!
#define servoZeroZ 165
Servo myservo;
byte pos;

//#define BAUD    (115200)
#define BAUD 115200

// These will be used in the near future.
#define VERSION "00072"      // 5 caracters
#define ROLE    "ALL-IN-ONE" // 10 characters

#define stepsPerInchX 3800
#define stepsPerInchY 3800
#define stepsPerInchZ 3200
#define stepsPerInchA 3200
#define stepsPerInchB 3200
#define stepsPerInchC 3200
#define stepsPerInchU 3200
#define stepsPerInchV 3200
#define stepsPerInchW 3200

//#define minStepTime 25 //delay in MICROseconds between step pulses.
#define minStepTime 625

// step pins (required)
#define stepPin0 A0
#define stepPin1 A2
#define stepPin2 -1
#define stepPin3 -1
#define stepPin4 -1
#define stepPin5 -1
#define stepPin6 -1
#define stepPin7 -1
#define stepPin8 -1

// dir pins (required)
#define dirPin0 A1
#define dirPin1 A3
#define dirPin2 -1
#define dirPin3 -1
#define dirPin4 -1
#define dirPin5 -1
#define dirPin6 -1
#define dirPin7 -1
#define dirPin8 -1

// microStepping pins (optional)
#define chanXms1 -1
#define chanXms2 -1
#define chanXms3 -1
#define chanYms1 -1
#define chanYms2 -1
#define chanYms3 -1
#define chanZms1 -1
#define chanZms2 -1
#define chanZms3 -1
#define chanAms1 -1
#define chanAms2 -1
#define chanAms3 -1
#define chanBms1 -1
#define chanBms2 -1
#define chanBms3 -1
#define chanCms1 -1
#define chanCms2 -1
#define chanCms3 -1
#define chanUms1 -1
#define chanUms2 -1
#define chanUms3 -1
#define chanVms1 -1
#define chanVms2 -1
#define chanVms3 -1
#define chanWms1 -1
#define chanWms2 -1
#define chanWms3 -1

#define xEnablePin A4
#define yEnablePin A5
#define zEnablePin -1
#define aEnablePin -1
#define bEnablePin -1
#define cEnablePin -1
#define uEnablePin -1
#define vEnablePin -1
#define wEnablePin -1

#define useEstopSwitch  false
#define usePowerSwitch  false
#define useProbe        false
#define useStartSwitch  false
#define useStopSwitch   false
#define usePauseSwitch  false
#define useResumeSwitch false
#define useStepSwitch   false

// Set to true if your using real switches for MIN positions.
#define useRealMinX false
#define useRealMinY false
#define useRealMinZ false
#define useRealMinA false
#define useRealMinB false
#define useRealMinC false
#define useRealMinU false
#define useRealMinV false
#define useRealMinW false

// Set to true if your using real switches for HOME positions.
#define useRealHomeX false
#define useRealHomeY false
#define useRealHomeZ false
#define useRealHomeA false
#define useRealHomeB false
#define useRealHomeC false
#define useRealHomeU false
#define useRealHomeV false
#define useRealHomeW false

// Set to false if your using real switches for MAX positions.
#define useRealMaxX false
#define useRealMaxY false
#define useRealMaxZ false
#define useRealMaxA false
#define useRealMaxB false
#define useRealMaxC false
#define useRealMaxU false
#define useRealMaxV false
#define useRealMaxW false

// If your using REAL switches you'll need real pins (ignored if using Virtual switches).
// -1 = not used.
#define xMinPin -1
#define yMinPin -1
#define zMinPin -1
#define aMinPin -1
#define bMinPin -1
#define cMinPin -1
#define uMinPin -1
#define vMinPin -1
#define wMinPin -1

#define xHomePin -1
#define yHomePin -1
#define zHomePin -1
#define aHomePin -1
#define bHomePin -1
#define cHomePin -1
#define uHomePin -1
#define vHomePin -1
#define wHomePin -1

#define xMaxPin -1
#define yMaxPin -1
#define zMaxPin -1
#define aMaxPin -1
#define bMaxPin -1
#define cMaxPin -1
#define uMaxPin -1
#define vMaxPin -1
#define wMaxPin -1

#define powerSwitchIsMomentary true // Set to true if your using a momentary switch.
#define powerPin    A0 // Power switch. Optional
#define powerLedPin -1 // Power indicator. Optional

#define eStopPin         A1 // E-Stop switch. You really, REALLY should have this one.
#define eStopLedPin      -1 // E-Stop indicator. Optional

#define probePin  A2 // CNC Touch probe input.     Optional
#define startPin  A3 // CNC Program start switch.  Optional
#define stopPin   A4 // CNC Stop program switch.   Optional
#define pausePin  A5 // CNC Pause program switch.  Optional
#define resumePin A6 // CNC Resume program switch. Optional
#define stepPin   A7 // CNC Program step switch.   Optional

// Spindle pin config
#define spindleEnablePin         -1 // Optional
#define spindleEnableInverted    false // Set to true if you need +5v to activate.
#define spindleDirection         -1 // Optional
#define spindleDirectionInverted false // Set to true if spindle runs in reverse.

#define spindleTach      -1 // Must be an interrupt pin. Optional.
                            // UNO can use pin 2 or 3.
                            // Mega2560 can use 2,3,18,19,20 or 21.

#define coolantMistPin   -1 // Controls coolant mist pump.   Optional
#define coolantFloodPin  -1 // Controls coolant flood pump.  Optional
#define powerSupplyPin   -1 // Controls power supply ON/OFF. Optional
#define powerSupplyInverted true // Set to "true" for +5v = ON
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

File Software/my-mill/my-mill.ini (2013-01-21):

# Generated by stepconf at Fri Nov  2 20:51:22 2012
# If you make changes to this file, they will be
# overwritten when you run stepconf again

[EMC]
MACHINE = hackCNC
DEBUG = 0

[DISPLAY]
DISPLAY = axis
EDITOR = gedit
POSITION_OFFSET = RELATIVE
POSITION_FEEDBACK = ACTUAL
MAX_FEED_OVERRIDE = 1.5
INTRO_GRAPHIC = linuxcnc.gif
INTRO_TIME = 1
PROGRAM_PREFIX = /home/linuxcnc/Documents
OPEN_FILE = /home/linuxcnc/HackCNC/Software/my-mill/hackCNC-text.ngc
INCREMENTS = 20mm 10mm 5mm 1mm 0.5mm


[FILTER]
PROGRAM_EXTENSION = .png,.gif,.jpg Greyscale Depth Image
PROGRAM_EXTENSION = .py Python Script
png = image-to-gcode
gif = image-to-gcode
jpg = image-to-gcode
py = python

[TASK]
TASK = milltask
CYCLE_TIME = 0.010

[RS274NGC]
PARAMETER_FILE = linuxcnc.var

[EMCMOT]
EMCMOT = motmod
COMM_TIMEOUT = 1.0
COMM_WAIT = 0.010
BASE_PERIOD =  100000
SERVO_PERIOD = 1000000

[HAL]
HALUI = halui
HALFILE = my-mill.hal
HALFILE = custom.hal
POSTGUI_HALFILE = custom_postgui.hal

[HALUI]
# add halui MDI commands here (max 64) 

[TRAJ]
AXES = 3
COORDINATES = X Y Z
LINEAR_UNITS = metric
ANGULAR_UNITS = degree
CYCLE_TIME = 0.010
DEFAULT_VELOCITY = 0.50
MAX_LINEAR_VELOCITY = 5.00
DEFAULT_LINEAR_VELOCITY = 5.0

[EMCIO]
EMCIO = io
CYCLE_TIME = 0.100
TOOL_TABLE = tool.tbl

[AXIS_0]
TYPE = LINEAR
HOME = 0.0
MAX_VELOCITY = 5.0
MAX_ACCELERATION = 6.0
STEPGEN_MAXACCEL = 7.5
SCALE = 1280
FERROR = 1
MIN_FERROR = 1
MIN_LIMIT = -0.1
MAX_LIMIT = 140.00
HOME_OFFSET = 0.0

[AXIS_1]
TYPE = LINEAR
HOME = 0.0
MAX_VELOCITY = 5.0
MAX_ACCELERATION = 6.0
STEPGEN_MAXACCEL = 7.5
SCALE = 1280
FERROR = 1
MIN_FERROR = 1
MIN_LIMIT = -0.1
MAX_LIMIT = 100.00
HOME_OFFSET = 0.0

[AXIS_2]
TYPE = LINEAR
HOME = 0.0
MAX_VELOCITY = 25.4
MAX_ACCELERATION = 15.0
STEPGEN_MAXACCEL = 18.75
SCALE = 25.0
FERROR = 0.1
MIN_FERROR = 0.1
MIN_LIMIT = -10.0
MAX_LIMIT = 10.0
HOME_OFFSET = 0.0

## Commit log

2012-11-02 Initial Commit
    Added Readme file and 3D Prints directory to store all the 3d printed
    parts.
    [5mm pulley.stl, 8mm pulley.stl, Carriage 1.stl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]
2012-11-09 Added support software
    [custom.hal, custom_postgui.hal, my-mill.hal]
2012-11-09 Added simple servo calibrator
2012-11-14 John's configuration
    [custom.hal, custom_postgui.hal, my-mill.hal]
2012-11-14 removed parallel stuff
    [my-mill.hal]
2012-11-14 moved ino into arduino friendly place
2012-11-14 Started modifying arduino sketch for servos
2012-11-21 Working firmware, barest software doco.
    [custom.hal, custom_postgui.hal, my-mill.hal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]
2012-11-25 Added dxf file for frame
    [hackCNC.dxf]
2012-11-25 Moved 3d print quantities to a more appropriate location
2012-12-04 Branch to CNCPlotter Board
2012-12-06 Updated Pins, stepping calcs, and changed digitalwritefast lib to interrupt safe version.
2012-12-13 Finer servo control added.
2012-12-13 Updated to use flat edged steppers
    [5mm pulley.stl, shaft adapter.stl]
2012-12-15 Added axis 0 ishomed option.
    [custom.hal]
2012-12-16 Getting fancy with the LCD.
    The LCD now updates independently for eStop and Power instructions.
2012-12-16 Run States and start of FB
    [custom.hal]
2012-12-28 Changed down to only supporting 3 axis
    [custom.hal]
2012-12-29 Added the pinouts for Luke's board
2013-01-01 changed to mm
    [my-mill.ini]
2013-01-08 These should be changes to make mm work. testing
    [my-mill.ini]
2013-01-11 Broken homing code. switching machines
    [EmcArduino_07b_32u4.ino]
2013-01-11 Hopefully fixed homing and x limits
    [EmcArduino_07b_32u4.ino]
2013-01-11 Added link to the HALUI documentation
    [custom.hal]
2013-01-12 Assembly Manual
2013-01-15 Remove wiring.h, part of Arduino.h since 1.0
2013-01-16 Making a mess, moving files
    Sorry guys.
    [5mm pulley.stl, 8mm pulley.stl, Carriage 1.stl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]
2013-01-16 Fixing the negative home error
    [EmcArduino_07b_32u4.ino]
2013-01-21 Fixed min home section
    [EmcArduino_07b_32u4.ino]
2013-01-21 z axis the right way up. Home really fixed now
    mis-labeled the previous one.
    [EmcArduino_07b_32u4.ino]
2013-01-22 Add arduino-mk Makefile for non-Arduino-IDE users
2013-01-22 Move step instructions to Timer3 interrupt for smoother stepping
2013-01-22 Possible fix for homing axes when at negative positions
    [EmcArduino_07b_32u4.ino]
2013-01-23 Fix offset used for homing to stop abusing x/y/zMin, allow Z axis to be homed in middle (thx John)
    [EmcArduino_07b_32u4.ino]
2013-01-23 fix to homing. idle indicator works.
    [EmcArduino_07b_32u4.ino]
2013-01-23 Updated assembly manual
